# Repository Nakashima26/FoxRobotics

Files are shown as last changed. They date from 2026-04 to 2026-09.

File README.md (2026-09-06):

# WRO 2026 — Future Engineers | Self-Driving Car

> **Team:** FoxRobotics
> **| Members:** Erick Blanco · Jesse Banda · César Emiliano Ahumada
> **| Coach:** Daniel Millan
> **| Country / Region:** México — Baja California
> **| Season:** 2026

---

## Table of Contents

1. [Vehicle Overview](#1-vehicle-overview)
   - [1.1 Design goals](#11-design-goals) · [1.2 Bill of Materials](#12-bill-of-materials)
2. [Mechanical Design & Mobility](#2-mechanical-design--mobility)
   - [2.1 Chassis selection](#21-chassis-selection) · [2.2 Wheels](#22-wheels) · [2.3 Drive system (torque vs. speed)](#23-drive-system-torque-vs-speed-analysis) · [2.4 Steering](#24-steering--rack-and-pinion-with-ackermann-geometry) · [2.5 Custom parts & assembly](#25-custom-parts--assembly)
3. [Power Architecture & Sensors](#3-power-architecture--sensors)
   - [3.1 Power budget](#31-power-budget) · [3.2 Sensor selection and placement](#32-sensor-selection-and-placement) · [3.3 PCB & wiring](#33-pcb--wiring)
4. [Software Architecture](#4-software-architecture)
   - [4.1 System overview](#41-system-overview--two-controllers-one-link) · [4.2 Inter-controller protocol ("V2")](#42-inter-controller-protocol-v2) · [4.3 Vision pipeline](#43-vision-pipeline-raspberry-pi--pure_pursuit) · [4.4 Obstacle handling](#44-obstacle-handling-obstacle-challenge) · [4.5 ESP32 state machine](#45-esp32-finite-state-machine-srcesp32purepursuitpurepursuitino) · [4.6 Cascade PID](#46-cascade-pid-always-running-underneath) · [4.7 Startup handshake](#47-startup-handshake) · [4.8 Development status](#48-development-status)
5. [Systemic Thinking & Engineering Decisions](#5-systemic-thinking--engineering-decisions)
   - [5.1 Subsystem interaction map](#51-subsystem-interaction-map) · [5.2 Key engineering trade-offs](#52-key-engineering-trade-offs) · [5.3 Iteration log](#53-iteration-log) · [5.4 Risk analysis](#54-risk-analysis) · [5.5 Failure & Incident log](#55-failure--incident-log)
6. [Testing & Validation](#6-testing--validation)
   - [6.1 How we test](#61-how-we-test) · [6.2 Results to date](#62-results-to-date) · [6.3 Validation matrix](#63-validation-matrix) · [6.4 Pre-run checklist](#64-pre-run-checklist-each-venue) · [6.5 Milestones](#65-milestones)
7. [How to Build & Run](#7-how-to-build--run)
   - [7.1 Hardware](#71-hardware-requirements) · [7.2 ESP32 firmware](#72-esp32-firmware) · [7.3 Raspberry Pi software](#73-raspberry-pi-software) · [7.4 Calibration](#74-calibration-before-each-venue) · [7.5 Run](#75-run) · [7.6 Autostart & deployment](#76-autostart--deployment)
8. [Repository Structure](#8-repository-structure)
9. [Videos](#9-videos)
10. [Photos](#10-photos)

**Companion document:** [Engineering Journal](ENGINEERING_JOURNAL.md) — the dated, phase-by-phase build log, from the pre-repo design work through today, tied to commits. [§5.3 Iteration log](#53-iteration-log) and [§6.5 Milestones](#65-milestones) are the thematic views of the same history.

---

# 1. Vehicle Overview

<p align="center">
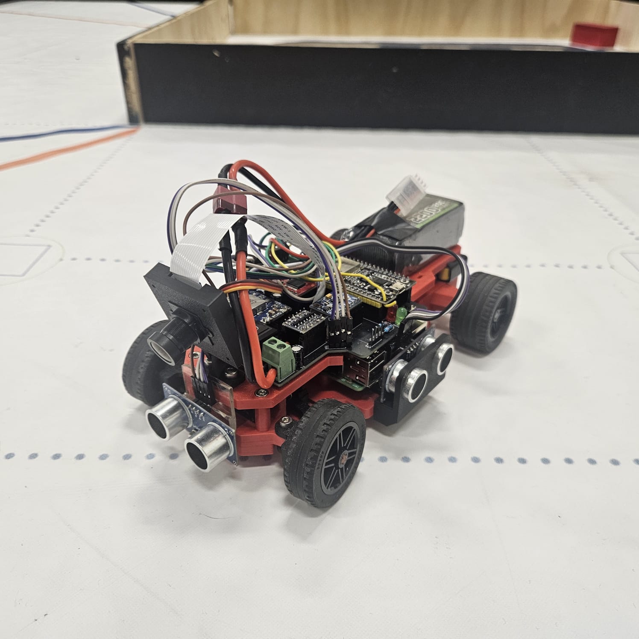
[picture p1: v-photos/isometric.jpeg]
Isometric view of the vehicle
  
</p>

Our vehicle is a custom-built autonomous car for the WRO 2026 Future Engineers — Self-Driving Cars challenge. It completes 3 laps around a randomized track, and in the Obstacle Challenge it also detects and correctly passes coloured traffic-sign pillars (**red → keep the pillar on the car's left / pass on its right; green → keep it on the right / pass on its left**) before parking at the end.

The car uses **two controllers working together**: a Raspberry Pi 4 runs the camera vision pipeline and the high-level path planner (Pure Pursuit), and an ESP32 runs the real-time control loop, the state machine and all the actuators. They talk over a UART link with a small line-based protocol ("V2"). This split is the central architectural decision of the project and is explained in [Section 4](#4-software-architecture) and [Section 5](#5-systemic-thinking--engineering-decisions).

**Key specifications:**

| Parameter | Value |
|---|---|
| Dimensions | 210 × 140 × 80 mm |
| Weight | 564 g |
| Drive type | Rear-wheel drive (RWD) |
| Steering | Ackermann rack-and-pinion, SG90 servo |
| High-level controller | Raspberry Pi 4 Model B (vision + Pure Pursuit) |
| Real-time controller | ESP32 DevKit (FSM, PID, motor & sensor I/O) |
| Inter-controller link | UART @ 115200 baud, line protocol "V2" (see §4.2) |
| Vision | Raspberry Pi Camera, NoIR wide-angle lens (FOV ≈ 120°), processed at 640 × 480 |
| Distance sensors | HC-SR04 (5V) × 3 — left, right, front — via 5V↔3.3V level shifter |
| IMU | MPU-6050 (gyroscope + accelerometer) |
| Drive motor | N20 DC gear motor (50:1) + 2:1 LEGO stage → 100:1 total |
| Motor driver | TB6612FNG |
| Battery | 3S LiPo 11.1 V 2200 mAh |
| Logic power | MINI560 step-down, 5 V |

## 1.1 Design goals

One reliable vehicle that finishes **both** challenges — scoring for completing three laps consistently over completing them fast. Everything below follows from that.

- **Fixed architecture from day one: Raspberry Pi 4 + ESP32.** The Pi does *all* image processing and vision; the ESP32 does *all* peripheral I/O — both sensing and actuation. This split was decided before the first line of code and never revisited.
- **Small footprint for maneuverability.** Comfortably inside the rulebook envelope with ~10 cm of margin on width and length — the car is ≈ 20 × 10 cm, deliberately smaller than the limit so it has room to maneuver in the obstacle field.
- **Mechanically extensible.** The chassis and the PCB were designed so components could be added later without a redesign. This paid off directly: the front ultrasonic — added for the obstacle-round segmented turn (see [§4.5](#45-esp32-finite-state-machine-srcesp32purepursuitpurepursuitino)) — went from idea to mounted-and-wired in under 30 minutes because both the chassis and the PCB already had the space and a spare header.
- **Tight-turn capable.** Rack-and-pinion steering driving both wheels symmetrically ([§2.4](#24-steering--rack-and-pinion-with-ackermann-geometry)) so the car can take the obstacle-round corners without a multi-point turn.
- **Room for a printed differential** so the rear wheels can turn at different speeds through a corner without scrub.
- **Electronics-first packaging.** The chassis was sized around the electronics — the Raspberry Pi 4 above all — and the PCB was then laid out to fit the finished mechanical model, not the other way around.

## 1.2 Bill of Materials

### Custom Manufactured Parts

| ID | Component | Description | Quantity | Supplier | Approximate Cost |
|---|---|---|---|---|---|
| 1 | BaseChasis | Main body of the vehicle. | 1 | Custom made, 3D printed | 1.6 USD |
| 2 | TopShell | Upper part of the vehicle. | 1 | Custom made, 3D printed | 1 USD |
| 3 | Cremallera | Rack used for steering. | 1 | Custom made, 3D printed | 0.1 USD |
| 4 | ServoGearDirection | Pinion for the steering system, directly connected to the servo. | 1 | Custom made, 3D printed | 0.5 USD |
| 5 | LinkageDirection | Linkage between the rack and steering knuckle. | 2 | Custom made, 3D printed | 0.05 USD |
| 6 | SteeringKnuckle | Allows lateral wheel movement for steering. | 2 | Custom made, 3D printed | 0.15 USD |
| 7 | DCsupport | Holds the DC motor in place. | 1 | Custom made, 3D printed | 0.05 USD |
| 8 | RingDifferential | Main driven gear of the differential that transfers power to the axle assembly. | 1 | Custom made, 3D printed | 0.25 USD |
| 9 | PlanetDifferential | Allows torque distribution between both wheels while enabling different wheel speeds during turns. | 2 | Custom made, 3D printed | 0.1 USD |
| 10 | PinionDifferential | Transfers rotational motion from the motor to the differential gear system. | 1 | Custom made, 3D printed | 0.1 USD |
| 11 | SunDifferential | Transfers torque from the differential gears to the wheel axle. | 2 | Custom made, 3D printed | 0.1 USD |
| 12 | CameraBase | Holds the camera frame in place. | 1 | Custom made, 3D printed | 0.1 USD |
| 13 | CameraBack | Rear section of the camera frame. Connects to the CameraBase. | 1 | Custom made, 3D printed | 0.1 USD |
| 14 | CameraFront | Camera frame. | 1 | Custom made, 3D printed | 0.2 USD |
| 15 | UltrasonicSupport | Holds an ultrasonic sensor in place (used for the left, right and front sensors). | 3 | Custom made, 3D printed | 0.3 USD |

---

### LEGO Components

| ID | Component | Description | Quantity | Supplier | Approximate Cost |
|---|---|---|---|---|---|
| 16 | Lego 6135494 | Front wheel axle. | 2 | LEGO | 0.8 USD |
| 17 | Lego 4535768 | Rear wheel axle. | 2 | LEGO | 1 USD |
| 18 | Lego 6121485 | Reduces friction on the rear wheels. | 2 | LEGO | 0.4 USD |
| 19 | Lego 4299389 | Rim for rear wheels. | 2 | LEGO | 1.2 USD |
| 20 | Lego 4184286 | Tires for rear wheels. | 2 | LEGO | 3.5 USD |
| 21 | Lego 6251174 | Rim for front wheels. | 2 | LEGO | 1.2 USD |
| 22 | Lego 6182551 | Tires for front wheels. | 2 | LEGO | 3.82 USD |

---

### Electronics

| ID | Component | Description | Quantity | Supplier | Approximate Cost |
|---|---|---|---|---|---|
| 23 | ESP32 | Real-time controller: sensor I/O, cascade PID, finite state machine, actuator PWM. | 1 | Unit Electronics | 8 USD |
| 24 | Raspberry Pi 4 Model B | High-level controller: computer vision and Pure Pursuit path planning. | 1 | Amazon | 60 USD |
| 25 | Mini560 5V | Step-down regulator powering the Raspberry Pi, ESP32 and peripherals. | 1 | Amazon | 6 USD |
| 26 | MPU 6050 | 6-axis IMU used to measure angular velocity and integrate heading. | 1 | Unit Electronics | 3 USD |
| 27 | HC-SR04 | Ultrasonic distance sensors — left, right (wall following) and front (obstacle-round cornering). | 3 | Unit Electronics | 10.5 USD |
| 28 | Level Shifter | Logic-level converter for the 5 V HC-SR04 echo lines into the 3.3 V ESP32. | 1 | Unit Electronics | 7 USD |
| 29 | Driver TB6612FNG | Motor driver controlling speed and direction of the DC drive motor. | 1 | Unit Electronics | 5 USD |
| 30 | RaspiCamera V2 | Camera module used for computer vision. | 1 | Amazon | 10 USD |
| 31 | Custom PCB | Printed circuit board for power distribution and electronic connections. | 1 | JLCPCB | 5 USD |

---

### Power System

| ID | Component | Description | Quantity | Supplier | Approximate Cost |
|---|---|---|---|---|---|
| 32 | Ovonic 2200mAh 3S | 3-cell LiPo battery powering the robot's electronics and drive system. | 1 | E-Bay | 13 USD |

---

### Actuators

| ID | Component | Description | Quantity | Supplier | Approximate Cost |
|---|---|---|---|---|---|
| 33 | N20 with 50:1 reduction | DC gear motor providing torque for robot movement. | 1 | Unit Electronics | 6 USD |
| 34 | SG90 Servo | Micro servo motor used for steering control. | 1 | Unit Electronics | 6 USD |

---

### Fasteners

| ID | Component | Description | Quantity | Supplier | Approximate Cost |
|---|---|---|---|---|---|
| 35 | M3 Screws | Used for structural assembly and component mounting. | 23 | Local Hardware Store | 1 USD |
| 36 | M3 Nuts | Used to secure structural and electronic components. | 1 | Local Hardware Store | 0.05 USD |
| 37 | M2 Nuts | Used to secure servo motor and servo pinion | 3 | Local Hardware Store | 0.15 USD |

### Total Estimated Cost

| Total |
|---|
| ~155 USD |

---

# 2. Mechanical Design & Mobility

### 2.1 Chassis selection

The chassis was designed from scratch to fit all the components we needed for competition. We printed it in red and black SUNLU PLA on a Bambu Lab A1, keeping the structure as light as possible without sacrificing the rigidity the drivetrain and electronics require.

For wheel transmission shafts, we used LEGO axles throughout: part 6135494 for the front and part 4535768 for the rear. This wasn't an aesthetic choice — LEGO axles have much better dimensional consistency than fully printed shafts, which flex under load and cause alignment issues. We also added LEGO bushings (6121485) to the rear axle to cut down on friction between moving parts.

| Component | Material / Part | Purpose |
| --- | --- | --- |
| Chassis | SUNLU PLA | Main robot structure |
| Front Axles | LEGO 6135494 | Power transmission |
| Rear Axles  | LEGO 4535768 | Rear drivetrain support |
| Bushings | LEGO 6121485 | Friction reduction |
| Printer | Bambu Lab A1 | Manufacturing process |

We used PLA because it prints fast, doesn't warp like ABS, and is stiff enough for indoor competition conditions. PETG has better impact resistance and ABS handles heat better, but neither of those properties matters much for a robot running on a flat mat indoors. What did matter was being able to iterate quickly and get consistent parts, and PLA delivered on both.

### 2.2 Wheels

We tested several wheel options before settling on LEGO parts. The rear wheels use rim 4299389 with tire 4184286, and the front uses rim 6251174 with tire 6182551. Both have a 43 mm outer diameter, which keeps the ride height even front to rear.

Since the drivetrain already uses LEGO axles, LEGO-compatible rims were the obvious fit — they mount directly without adapters, which removes a potential source of wobble at the wheel interface.

The 43 mm diameter was also validated against our motor RPM target. At our gear ratio, this diameter puts normal operation in the 40–70% PWM range, which gives us enough resolution for smooth speed control. A noticeably larger wheel would push operating duty cycles above 85% and compress the usable throttle range.

We ran the car at full throttle on the competition mat surface and saw no detectable slip at the rear. The LEGO rubber compound grips the white matte WRO field without any prep needed.

### 2.3 Drive system (torque vs. speed analysis)

The main drive is an N20 DC motor with a 50:1 internal gearbox — compact at 12 × 10 × 26 mm and still enough torque for a ~1.5 kg vehicle. Between the motor output shaft and the differential, we added a 2:1 LEGO gear stage, bringing the total drivetrain reduction to **100:1** and estimated rear axle torque to about 1.76 kg·cm.

**Why 100:1 and not just 50:1?**

We ran the 50:1 configuration first. It was faster, but corner exits were inconsistent — the rear wheels would occasionally lose traction under acceleration, causing yaw disturbances the PID couldn't fully catch. At 100:1, top speed dropped but torque delivery became smooth and predictable all the way through the speed range. Corner exits became repeatable, which turned out to be a prerequisite for reliable PID tuning.

The ratio also keeps the motor in its efficient RPM band during most of the run, which matters because the motor shares a power source with the logic rail.

The car completes all three Open Challenge laps in about 12 seconds at just 60% motor speed. That headroom is useful if we need to push speed in later iterations.

**The takeaway:** we prioritized consistency over raw speed. A robot that reliably finishes 3 laps scores more than one that's faster but unpredictable.

### 2.4 Steering — rack-and-pinion with Ackermann geometry

Steering is controlled by an SG90 servo connected to both front knuckles through a rack-and-pinion mechanism with symmetric tie rods.

**Mechanism specs:**

| Parameter | Value |
|---|---|
| Servo | SG90 (0°–180° range) |
| Firmware straight-ahead trim | 80° (servo-horn spline offset; `centroServo` in firmware) |
| Pinion | Module 1, 14 teeth |
| Pinion pitch diameter | 14 mm (dp = m × z = 1 × 14) |
| Pinion outer diameter | 16 mm (dp + 2×addendum = 14 + 2) |
| Rack | Module 1, 11 teeth, 27.5 mm total travel |
| Rack displacement per servo degree | 0.1222 mm/° |
| Transmission ratio | 2.50° servo : 1° wheel |
| Geometric wheel steering range | ±43° from center |
| Firmware-clamped servo command | 20°–150° (≈ ±35° usable at the wheel) |

**Kinematic analysis:**

The 14 mm pitch diameter gives a pitch circumference of 43.98 mm. Each degree of servo rotation moves the rack 0.1222 mm. At 90° per side from center, the rack travels 11.00 mm per side — producing ±43° at the front wheels.

The outer diameter of 16 mm confirms the module (d_outer = dp + 2×m = 14 + 2 = 16 mm).

The 2.50:1 ratio reduces steering sensitivity at the wheel, which gives the inner control loop finer resolution at its update rate. A lower ratio would make steering response too abrupt.

The firmware never commands the full mechanical range: `escribirServo()` is clamped to 20°–150° (about ±35° at the wheel) so a saturated control output can't drive the rack into its physical end stop. That still clears the tightest Open-Challenge corridor (600 mm) and the maneuvering the Obstacle Challenge needs.

**Why rack-and-pinion over a direct servo arm?**

A direct arm only controls one wheel directly. The opposite knuckle, linked by a fixed-length tie rod, gets an angle that's geometrically correct only at center — producing toe error everywhere else. The rack pushes both tie rods symmetrically, so both wheels get the right angle at every steering position. Combined with the Ackermann geometry of the knuckles, each wheel tracks its own correct turning radius. No lateral scrub, and steering response is linear across the full range.

### 2.5 Custom parts & assembly

Every structural part is 3D-printed in SUNLU PLA on a Bambu Lab A1. The mechanical model was built first; the PCB was then laid out to fit it. Editable SolidWorks parts are in [`models/CAD/`](models/CAD/), printable meshes in [`models/STL/`](models/STL/), isometric renders in [`models/renders/`](models/renders/).

<p align="center">
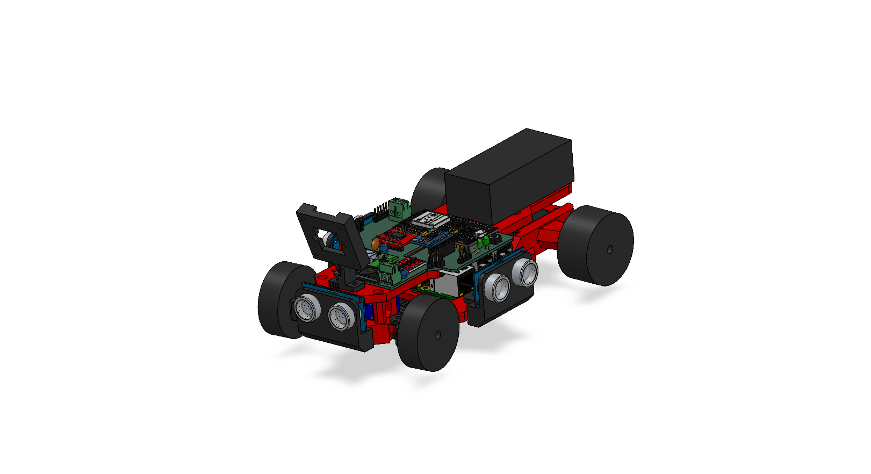
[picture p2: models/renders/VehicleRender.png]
Full vehicle CAD assembly
  
</p>

| Render | Part | Function / design note |
|---|---|---|
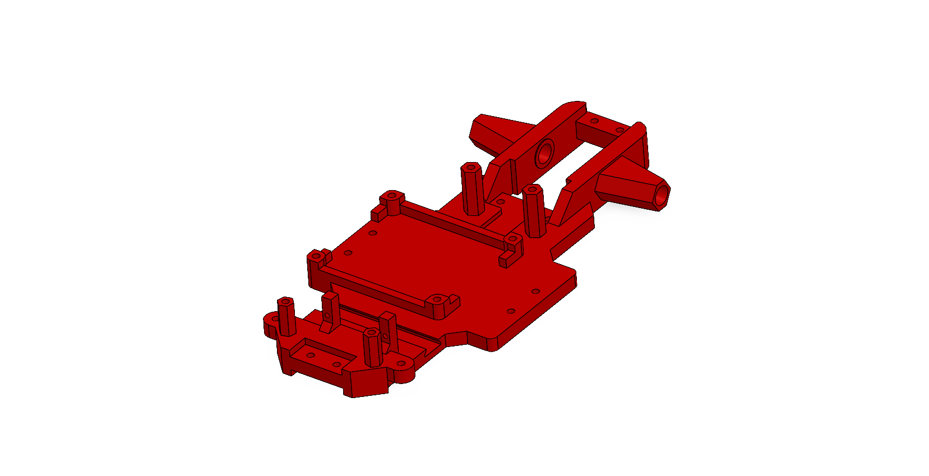
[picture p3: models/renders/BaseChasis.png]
BaseChasis render
|  | **BaseChasis** | Main structure. Sized around the electronics (Raspberry Pi 4 first); carries the PCB, steering, drivetrain and every sensor mount. |
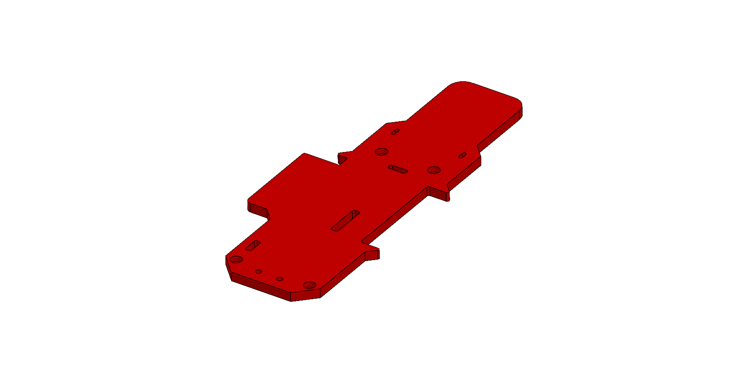
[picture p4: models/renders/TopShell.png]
TopShell render
|  | **TopShell** | Top cover — closes the electronics bay and protects the wiring. |
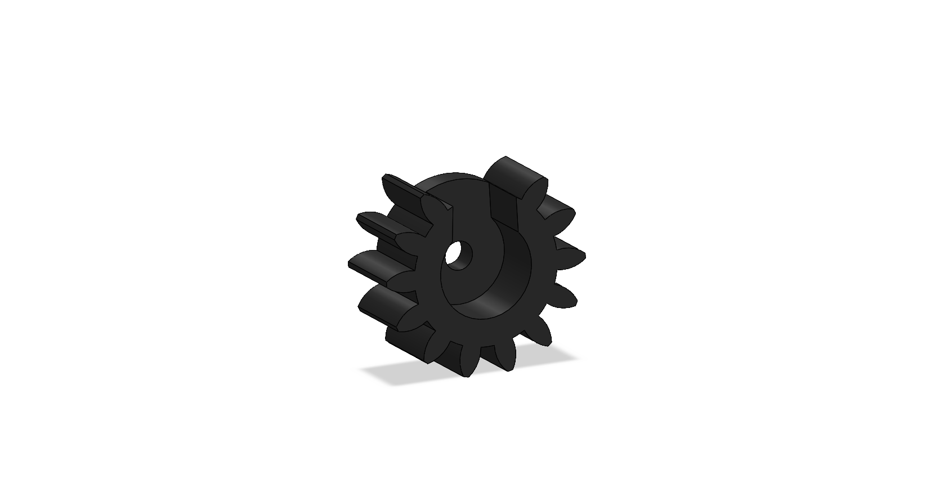
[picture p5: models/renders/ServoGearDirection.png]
ServoGearDirection render
|  | **ServoGearDirection** | Pinion pressed onto the SG90 output shaft — module 1, 14 teeth. |
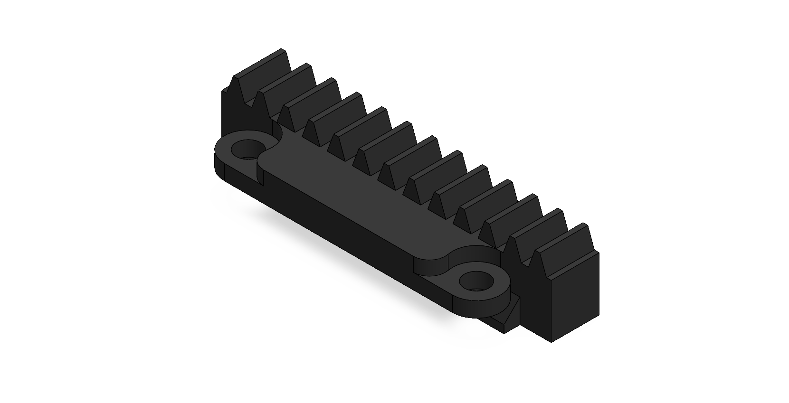
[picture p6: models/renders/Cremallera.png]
Cremallera render
|  | **Cremallera** (rack) | Module 1, 11 teeth, 27.5 mm travel. Converts servo rotation into lateral travel for the tie rods. |
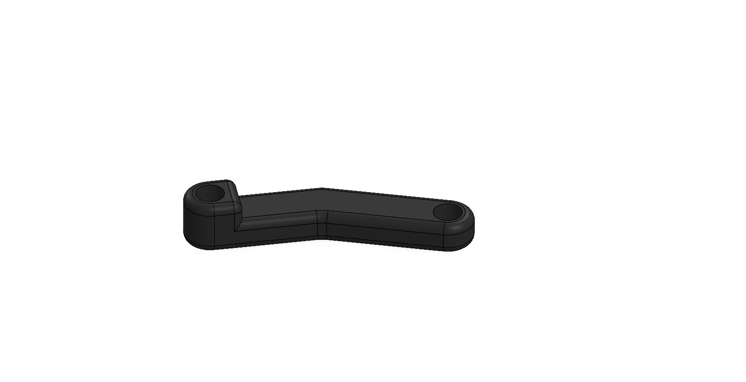
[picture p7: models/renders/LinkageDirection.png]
LinkageDirection render
|  | **LinkageDirection** ×2 | Tie rods from the rack ends to the steering knuckles — symmetric, so both wheels get the correct angle at every rack position. |
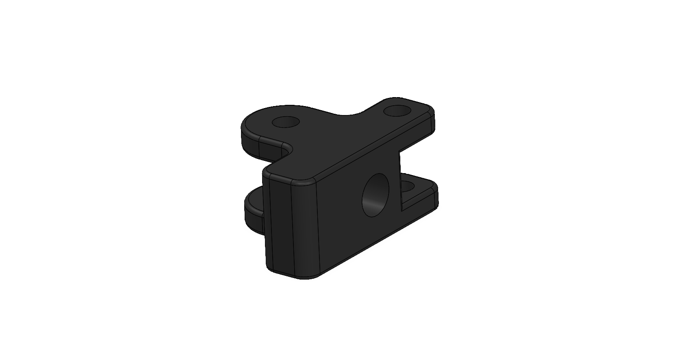
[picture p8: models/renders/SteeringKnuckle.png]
SteeringKnuckle render
|  | **SteeringKnuckle** ×2 | Front-wheel pivots; their geometry sets the Ackermann steering angles. |
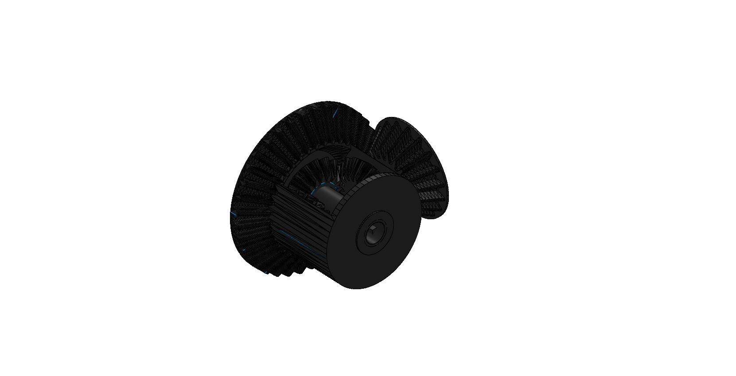
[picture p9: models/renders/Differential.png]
Differential render
|  | **Differential** (Ring / Planet ×2 / Pinion / Sun) | Printed open differential — lets the rear wheels turn at different speeds through a corner. |
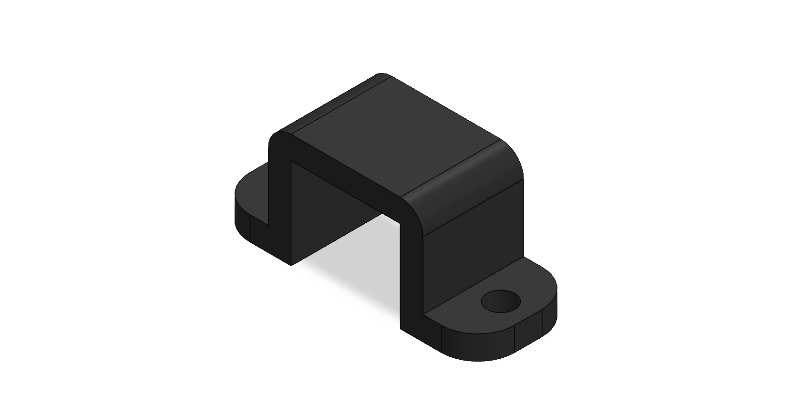
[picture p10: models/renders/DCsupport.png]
DCsupport render
|  | **DCsupport** | Mounts the N20 gear motor to the chassis. |
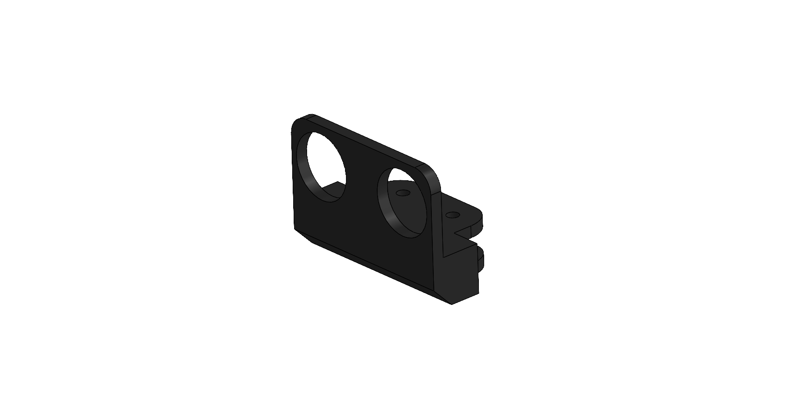
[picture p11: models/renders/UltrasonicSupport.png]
UltrasonicSupport render
|  | **UltrasonicSupport** ×3 | Two identical side mounts; one slightly smaller front mount, added later for the obstacle-round segmented turn. |
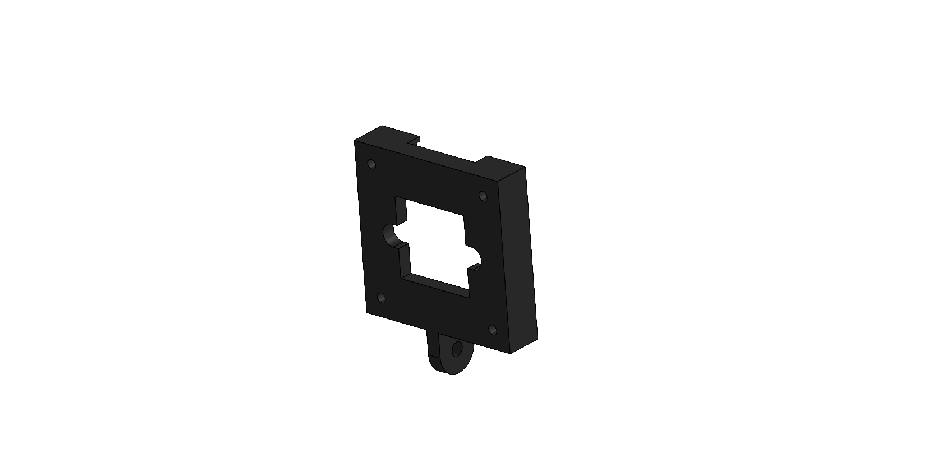
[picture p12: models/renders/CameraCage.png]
Camera cage render
|  | **CameraHold** | Structure in charge of holding the camera. Sets the fixed ~15° downward tilt the BEV homography is calibrated against ([§3.2](#32-sensor-selection-and-placement)). |

#### Assembly order

1. **Chassis base** — the reference part everything mounts to.
2. **Steering** — press the pinion onto the servo and seat the servo in the chassis; slide in the rack; link each rack end to a SteeringKnuckle with a LinkageDirection tie rod; fit the knuckles and the front LEGO axles.
3. **Drivetrain** — N20 motor into the DCsupport; assemble the printed differential; rear LEGO axles with bushings.
4. **Sensor mounts** — the two side UltrasonicSupports (identical) and the smaller front one; the camera cage (base + back + front) with the camera.
5. **Electronics** — PCB onto the chassis bosses; wire the Pi 4, ESP32, the three HC-SR04 (through the level shifter), the MPU-6050, the TB6612 + motor, the servo, and the start button + status LED.
6. **TopShell** — close the bay.

All fasteners are M3 (M2 nuts on the servo horn and pinion).

---

# 3. Power Architecture & Sensors

### 3.1 Power budget

The whole vehicle runs off an Ovonic 2200mAh 3S LiPo. Power splits two ways: the motor driver takes battery voltage directly for the DC motor, and everything else goes through a MINI560 step-down converter producing a stable 5V at up to 5A.

| Rail | Source | Consumers | Max Current Draw |
|---|---|---|---|
| 5V Logic | MINI560 Step-Down Converter | Raspberry Pi 4 + RaspiCam V2, ESP32, HC-SR04 ×3, MPU6050, SG90 | ~4.0 A |
| Battery / Main Power | Ovonic 2200mAh 3S LiPo | Entire vehicle power distribution | ~35 A discharge capability |
| Motor Power | Motor Driver directly from 3S LiPo | DC drive motor | ~1.6 A peak |
| 3.3V Internal | ESP32 internal regulator | I²C communication and internal ESP32 logic, Level Shifter | ~200 mA |

The Ovonic battery is rated 120C continuous, which is theoretically 264 A. We're drawing about 4.5 A peak — under 2% of its discharge capability. There's no shortage of headroom here.

The Raspberry Pi and the ESP32 share the 5 V rail but the DC motor is fed straight from the battery through the TB6612FNG, so stall-current spikes on the motor never sag the logic supply.

### 3.2 Sensor selection and placement

| Sensor | Purpose | Placement | Notes |
|---|---|---|---|
| Raspberry Pi Camera Module V2 | Lane, corner-line and pillar detection | Front-center, ~15° downward tilt | Main vision system, OpenCV on the Pi |
| HC-SR04 (left) | Left wall distance | Left side of the chassis | Feeds the wall-centering PID |
| HC-SR04 (right) | Right wall distance | Right side of the chassis | Feeds the wall-centering PID |
| HC-SR04 (front) | Distance to the wall ahead when approaching a corner | Front bumper, facing forward | Obstacle round only — triggers the CRUCERO → MANIOBRA sequence |
| MPU-6050 | Heading integration during cornering and recovery | Center of chassis | Gyro Z integrated into `anguloGyro`, echoed back to the Pi |

#### Camera system

The camera handles lane geometry (via a bird's-eye-view transform), the orange corner-line markers, and red/green pillar detection. Image processing runs on the Raspberry Pi 4 with OpenCV in real time and drives the Pure Pursuit planner.

It is mounted front-center with a ~15° downward tilt. We tested a horizontal mount first, but that captured too much background, which slowed detection and added noise. Tilting it down focuses the field of view on the track and the obstacle zone, which cut both false positives and computational load. The exact tilt is baked into the bird's-eye-view homography during calibration (see §4.3), so the mount must not move after calibration.

The lens is a wide-angle **NoIR** unit (~120° FOV), chosen over the original ~63° lens so the camera sees far enough ahead to react to a pillar and read the corner on the same frame. The wide lens ships without an IR-cut filter, which gave the raw image a heavy red cast and broke every HSV mask. The libcamera capture pipeline pins white-balance instead of letting it float — `libcamerasrc awb-enable=false colour-gains=<1.2,1.5>` — so the correction holds across venue lighting, and the pillar HSV ranges were re-tuned on the corrected image (see [ERR-03](#err-03--wide-angle-noir-lens-put-a-red-cast-on-every-frame)).

#### HC-SR04 ultrasonic sensors

The left and right sensors drive lateral positioning and wall following. The **front** sensor was added for the Obstacle Challenge: because that round uses a segmented, stop-and-maneuver turn instead of a continuous arc (see §4.5), the car needs to know how far it is from the wall ahead so it can decide *when* to stop cruising and *which* maneuver (forward arc or reverse pivot) to run.

We originally tested VL53L0X time-of-flight sensors. On paper they win — ±3 mm accuracy versus ±15 mm for the HC-SR04, and a narrower beam. In practice, the black competition walls absorbed their 940 nm IR signal and consistently returned out-of-range readings at 300 mm. The HC-SR04 reflects off any surface regardless of color. We went with reliability over precision and made up the accuracy difference with software filtering (EMA on all three channels, plus a 5-sample median on the front channel to reject spikes before they can trigger a maneuver).

#### MPU-6050 IMU

The MPU-6050 gives heading and rotation data during cornering and recovery. The gyro Z axis is integrated each loop into `anguloGyro`, with a 1°/s deadband to suppress MEMS thermal drift on straights. On startup the firmware averages several hundred stationary samples to compute the gyro bias (`calcGyroOffsets`); if that offset comes back unusually large the firmware halves the integration scale as a safety net. The integrated heading is also sent back to the Pi in every acknowledgement so the vision side can dead-reckon obstacle positions (see §4.4).

### 3.3 PCB & wiring

A custom two-layer PCB is the vehicle's backplane: it distributes power and carries every signal line between the ESP32, the sensors and the motor driver, so there is no breadboard or flying-wire harness to work loose. This is what let the front ultrasonic go in in under 30 minutes ([§1.1](#11-design-goals)) — the header was already there. The full editable KiCad project is in [`electrical/WRO_RevA/`](electrical/WRO_RevA/).

**Schematic** ([`schemes/schematic.png`](schemes/schematic.png)):

<p align="center">
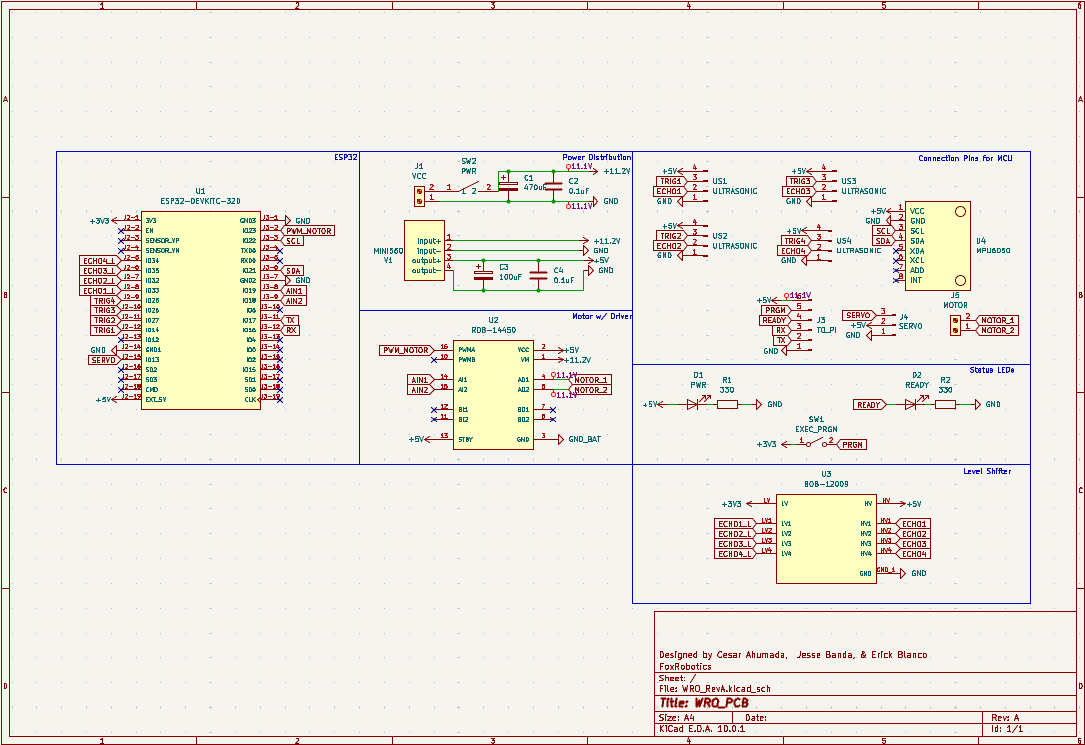
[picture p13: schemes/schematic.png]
KiCad schematic
  
</p>

The ESP32 DevKit (`U1`) sits at the centre. Battery voltage (~11.1 V, 3S) comes in at the `VCC` screw terminal (`J1`) and splits two ways: the motor driver takes it directly, and a MINI560 buck (`V1`, bulk caps `C1`–`C4`) drops it to the 5 V logic rail. The RDB-14450 driver (`U2`) takes `PWM_MOTOR` / `AIN1` / `AIN2` from the ESP32 and drives `MOTOR_1/2` out to the screw terminal `J5`. The four HC-SR04s land on headers `US1`–`US4` (5 V / TRIG / ECHO / GND); their 5 V echo lines return through a BOB-12009 level shifter (`U3`) that steps `ECHO1`–`ECHO4` down to 3.3 V for the ESP32. The MPU-6050 (`U4`) is on I²C. The `TO_PI` header (`J3`) is the entire link to the Raspberry Pi — `RX` / `TX` for the V2 protocol, `READY` for the handshake, `PRGN` for the start button (`SW1`), plus 3.3 V / GND. Two status LEDs (`D1` PWR, `D2` READY) complete the operator interface from [§4.7](#47-startup-handshake).

**Populated board** ([`schemes/pcb_render.png`](schemes/pcb_render.png)):

<p align="center">
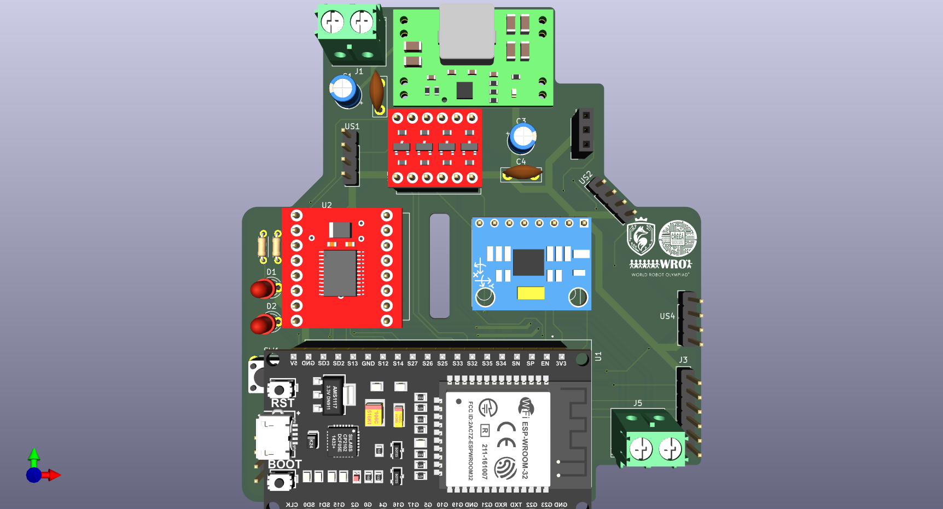
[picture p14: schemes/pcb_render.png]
3D render of the populated PCB
  
</p>

**Board outline** ([`electrical/PCB_dimensions.png`](electrical/PCB_dimensions.png)):

<p align="center">
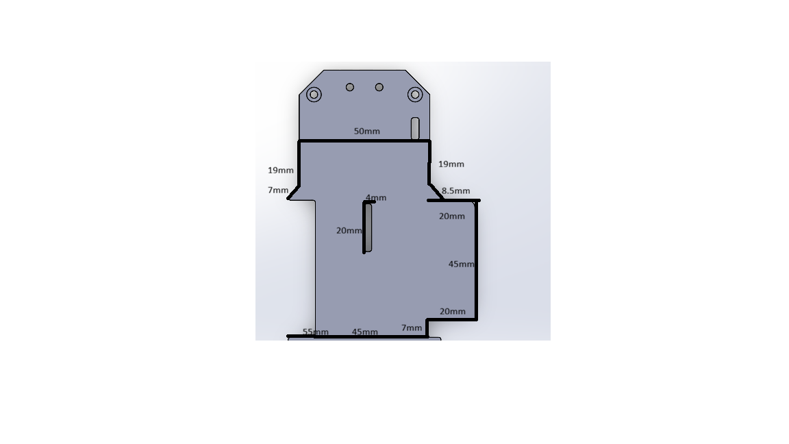
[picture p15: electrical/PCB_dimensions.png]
PCB outline and dimensions
  
</p>

The board is a custom non-rectangular shape (~55 mm at its widest) that nests into the chassis around the Raspberry Pi 4 and the drivetrain — the electronics-first packaging from [§1.1](#11-design-goals) in physical form. The cut-outs and the mounting-hole row let the PCB, the steering and the sensor mounts share one footprint without stacking height.

---

# 4. Software Architecture

### 4.1 System overview — two controllers, one link

Responsibility is split across two processors by hardware strength:

```
        RASPBERRY PI 4 (Python, OpenCV)                          ESP32 (Arduino / C++)
 ┌───────────────────────────────────────────┐    V2     ┌────────────────────────────────────┐
 │ Camera → BEV homography → floor centerline│   UART    │ readPiSerial()  →  parse V2        │
 │ Pillar detection (HSV) + corner-line track│  ──────►  │                                    │
 │ Rolling obstacle memory (dead reckoning)  │  115200   │ 6-state FSM                        │
 │ Pure Pursuit geometric controller         │           │  SIGUIENDO / GIRANDO / RECUPERANDO │
 │ RECUPERANDO trigger (measured state)      │  ◄──────  │  CRUCERO / MANIOBRA / TERMINANDO   │
 │ builds one V2 line per processed frame    │  ACK:V2   │ cascade PID (wall + gyro)          │
 └───────────────────────────────────────────┘   ang=    │ servo + motor PWM, HC-SR04, MPU    │
                                               est= dir= └────────────────────────────────────┘
```

- The **Pi** decides *where to steer*: it turns the camera frame into a top-down view, extracts a drivable centerline, runs a Pure Pursuit controller against it, and reduces the result to a single normalized steering value plus a few status flags. It processes 1 of every 3 captured frames (~12–15 Hz effective).
- The **ESP32** decides *how to drive*: it owns the 50 Hz control loop, the finite state machine, corner detection, the recovery behaviour, and every actuator. In the Obstacle round it treats the Pi's steering value as the primary reference while Pure Pursuit is active, and falls back to its own wall + gyro PID if the Pi goes silent for more than 800 ms. In the Open round it ignores the Pi's steer altogether and runs on wall + gyro PID the whole time (§4.5).

Why not one processor? Real-time GPIO timing (ultrasonic pulses, servo/motor PWM, gyro sampling) and non-deterministic OpenCV latency don't coexist well on one core. Linux can't guarantee a µs-accurate pulse while an HSV pass is running; a microcontroller can't run OpenCV. Splitting them lets each run at its own natural rate, and a late UART packet just means the ESP32 reuses the last command instead of stalling. This trade-off is analyzed in [Section 5](#5-systemic-thinking--engineering-decisions).

**Where to start reading the code:** the Pi loop is [`pure_pursuit/runtime_nuevo.py`](src/RASPI/cam/pure_pursuit/runtime_nuevo.py) (`run()` → per-frame block); the ESP32 loop is [`PurePursuit.ino`](src/ESP32/PurePursuit/PurePursuit.ino) (`loop()` → the `switch (estado)`). Every module is annotated in [Section 8](#8-repository-structure); tunables live in [`pure_pursuit/config.py`](src/RASPI/cam/pure_pursuit/config.py).

### 4.2 Inter-controller protocol ("V2")

One line per processed frame, newline-terminated, 115200 baud. The rest of Section 4 refers to these fields by name.

**Pi → ESP32:**

```
V2,obs=+0.123,turn=0,state=pp,prio=1,mem=18,pp=1,pasado=0,intr=0
```

| Field | Meaning |
|---|---|
| `obs` | Normalized steering, `steer_deg / 60`, range −1…+1 (`+` = right). |
| `turn` | Legacy directional hint — always `0`; turn direction is resolved on the ESP32 side. |
| `state` | Human-readable label for the journal (e.g. `pp`, `avoid_red`). |
| `prio` | `1` = an obstacle is actively being avoided → **ESP32 must not start a corner turn**. |
| `mem` | Frames of obstacle memory still live → also blocks corner detection while `> 0`. |
| `pp` | `1` = Pure Pursuit steering is authoritative (suspend the wall PID). |
| `pasado` | One-frame pulse: the Pi confirms the car has *physically* cleared an obstacle → enter RECUPERANDO. |
| `intr` | Interior-pass flag (disabled by default). |

**ESP32 → Pi:**

```
ACK:V2,ang=12.34,est=S,dir=L,...debug...
```

| Field | Meaning |
|---|---|
| `ang` | Integrated IMU heading `anguloGyro` (degrees); resets to 0 at each turn. |
| `est` | FSM state — `S` SIGUIENDO, `G` GIRANDO **or** MANIOBRA, `R` RECUPERANDO, `C` CRUCERO. |
| `dir` | Track turn direction — `?` until the first turn, then `L` / `R`. |

### 4.3 Vision pipeline (Raspberry Pi — `pure_pursuit/`)

Entry point: `pure_pursuit/runtime_nuevo.py`. Per processed frame:

1. **Capture** — a threaded grabber pulls frames from the Pi camera through a libcamera/GStreamer pipeline at 640 × 480 BGR, dropping stale buffers so the loop always sees the newest frame.
2. **Bird's-eye view (`bev.py`)** — a homography (inverse-perspective mapping) warps the camera frame to a top-down 400 × 400 image at 2 mm/px. The homography comes from `bev_calib.npz`, generated once by `calibrate.py` from a **3 × 3 grid of 9 physical floor markers** (RANSAC fit). We use 9 points, not the minimum 4: a 4-point fit is exact and can't detect a mis-click or extrapolate safely beyond the marked area, while 9 points let the solver average out click noise across the full range the centerline actually uses (from just ahead of the car out to ~550 mm).
3. **Pillar detection (`vision.py`)** — HSV masks for red and green, then contour filtering by area, **solidity** (compact blob ≈ 0.7–0.9, painted line < 0.4) and **aspect ratio** (< 2.2) so the mat's coloured lines are not mistaken for pillars.
4. **Centerline (`centerline.py`)** — a floor-colour mask in the BEV, minus inflated "keep-out" disks around each obstacle. The keep-out is **asymmetric per the WRO rule**: a red pillar inflates further to its *left* (car passes on the right), a green pillar further to its *right*. Rows are sampled bottom-to-top; each row blends the free-gap center with the WRO pass-side using a weight that ramps up as the car nears the can (not a binary switch). A 1-D moving average plus a per-step Δx clamp keep the path within the servo's curvature limit.
5. **Pure Pursuit (`controller.py`)** — a geometric pure-pursuit controller in BEV pixel space. Look-ahead is **adaptive**: it shrinks from 100 px toward 78 px as the nearest can closes *longitudinally*, so the car keeps translating and arcs around the can instead of pivoting in place. Output is slew-limited to 6°/frame to kill frame-to-frame steering whip.
6. **Serialize** — the steering angle is normalized (`obs = steer_deg / 60`) and packed into one V2 line with the status flags (§4.2).

```mermaid
flowchart TB
    A["Capture — threaded grabber<br/>Pi camera 640×480 BGR, drops stale buffers"]
    B["BEV homography (bev.py)<br/>IPM warp to 400×400 top-down, 2 mm/px<br/>from bev_calib.npz (9-point RANSAC)"]
    C["Pillar detection (vision.py)<br/>HSV red/green + area + solidity + aspect ratio"]
    D["Centerline (centerline.py)<br/>floor mask minus asymmetric keep-out disks<br/>red inflates left, green inflates right<br/>pass-side weight ramps with distance"]
    E["Rolling obstacle memory (obstacle_memory.py)<br/>ego-motion: assumed speed + real IMU heading from ACK<br/>confidence decay, prune-on-pass"]
    F{"Measured RECUPERANDO trigger<br/>ARM / CLEAR / SKEW — see §4.4"}
    G["Pure Pursuit (controller.py)<br/>geometric, look-ahead 100 to 78 px adaptive<br/>slew-limited 6°/frame"]
    H["Serialize one V2 line<br/>obs = steer_deg / 60, plus prio / mem / pp / pasado"]
    A --> B
    B --> C
    B --> D
    C --> E
    E --> D
    E --> F
    D --> G
    G --> H
    F --> H
    H --> Z(["UART to ESP32 @ 115200"])
```

#### How the Pure Pursuit controller works

Pure Pursuit is a path-tracking method: instead of reacting to an *error signal*, the controller looks a fixed distance ahead along the path — the **look-ahead** — picks the point on the centerline at that distance, and computes the single steering angle whose turning arc, starting from the car's current pose, passes exactly through that point. Every frame the target point moves forward along the centerline and the car "chases" it, so the trajectory is always a smooth arc onto the path rather than a hand-tuned reaction curve.

```
          centerline (from BEV)                 look-ahead point picked at
        ·····•·····•·····•···•···•  ← target    distance  ld  along the path
                            ╲
                             ╲  arc the steering angle produces
              ┌───┐           ╲
              │car│────────────•   robot pose (rear axle = reference)
              └───┘
                 └─ α = bearing to target,  steer = atan2(2·L·sin α, ld)
```

Why it fits this problem:

- The vision pipeline already produces a **path** (the centerline), not a point to servo onto — Pure Pursuit consumes that path directly.
- The look-ahead is a single, physically meaningful tuning knob: **short = cut hard toward the path** (fast dodge), **long = ease onto it** (smooth cruise). That is exactly the behaviour the obstacle logic needs, so avoidance is folded into the *same* controller by shrinking the look-ahead near a can instead of adding a separate avoidance mode.
- It degrades gracefully: a noisy or short path just moves the target point a little; there is no integrator to wind up and no error term to spike.

```python
dx = target[0] - robot_x          # lateral offset to the look-ahead point (BEV px)
dy = robot_y - target[1]          # forward distance to it
ld = max(1.0, math.hypot(dx, dy)) # actual chord length
alpha     = math.atan2(dx, dy)                                   # bearing to the point
steer_rad = math.atan2(2.0 * C.WHEELBASE_PX * math.sin(alpha), ld)  # pure-pursuit arc
steer_deg = math.degrees(steer_rad)

if bev_obstacles:                                   # a can is in play
    steer_deg *= self._distance_steer_gain(...)     # ramp 0.30→1.0 as it closes
steer_deg = max(-C.MAX_STEER_DEG, min(C.MAX_STEER_DEG, steer_deg))
steer_deg = clamp(steer_deg, prev ± C.PP_STEER_SLEW_DEG)   # 6°/frame slew limit
```

`adaptive_lookahead` shrinks the look-ahead from 100 px toward 78 px, and `_distance_steer_gain` ramps the steering scale from 0.30 up to 1.0, both as the nearest can closes. Both key off the **longitudinal** distance to the can (forward gap), not the Euclidean one: a can still off to the side but level with the car used to keep those values relaxed, and the car drove straight past the point where it should have started turning. The WRO pass-side bias (right of red, left of green) is *not* handled here — it is already baked into the centerline by `centerline.py`, so the controller only has to follow the path it is given.

If `bev_calib.npz` is missing, the runtime falls back to a simple reactive PID on the pillar's x-position in the raw frame (`RED_TARGET_PX` / `GREEN_TARGET_PX`) so the car is never left without a controller.

### 4.4 Obstacle handling (Obstacle Challenge)

**Rolling obstacle memory (`obstacle_memory.py`).** The BEV only contains what the camera sees *now*; as the car closes on a can, the can leaves the bottom of the frame, its keep-out disc vanishes, and the centerline snaps back to center — cutting the corner onto the can. The memory fixes this: seen cans are stored as `(x, y, colour, confidence)` in robot-relative BEV coordinates and, every frame, the ego-motion is applied to every remembered can — forward travel from an assumed speed, rotation from the **real IMU heading change** in the ESP32 acknowledgement:

```python
dheading = heading_deg - self._prev_heading          # real Δ from the ACK, degrees
ds_px    = (C.ROBOT_SPEED_MMS * dt_s) / C.MM_PER_PX  # assumed forward advance, BEV px
# a hard dodge rotates the car without translating it — shrink ds_px when |dheading| is large
ds_px   *= turn_brake(dheading)
self._advance(ds_px, dheading)     # each can: y += ds_px, then rotate −dheading about the robot
```

Fresh detections are merged in, unseen cans decay in confidence and are pruned once genuinely passed. The inflated keep-out therefore persists until the car has physically cleared the can. The `heading_deg` this relies on is exactly the value the ESP32 integrates for its own control (see §4.6) and echoes back — one shared heading, so the map rotates by the same angle the car actually turned.

**"Mine" vs "beyond the corner" (`corner_lines.py`).** The mat's orange corner lines are tracked row-by-row in the BEV. Each remembered can is classified as *mine* (on my straight, must be avoided) or *beyond* (on the next straight, ignore for now), with asymmetric hysteresis — quick to start avoiding, slow to stop — because starting to dodge is the safe side of a wrong call.

**Far hint (`far_hint.py`).** A PD controller on a pillar's offset in the *raw* camera frame (before it projects into the BEV range) nudges the steering to pre-center on a distant can, capped at ±12° so it can only hint, never dodge.

**Mid-turn detector (`mid_turn.py`).** While the ESP32 is turning, the rolling memory is disabled (its motion model assumes forward travel, which a pivot violates). This detector instead uses only the raw per-frame BEV projections and requires a same-colour can in a consistent position across several frames inside a close forward cone to "confirm" it. **Phase 1 (current): observe and log only** — it writes `[MTURN]` lines to the journal and does not yet change steering, so we can measure its reliability on-track before wiring it into the firmware.

#### Triggering RECUPERANDO from the obstacle memory

**The problem.** When the car has to swing wide around a can with no room to spare, it finishes the pass **crooked** — pointing 30–60° off the straight — and often with one wall out of ultrasonic range. At that exact moment the camera view is the least trustworthy (the centerline is short and skewed), so letting Pure Pursuit "straighten itself" from what it sees tends to over- or under-correct into a wall. The fix is to hand the wheel to the ESP32's wall + gyro PID (state `RECUPERANDO`) until the chassis is realigned — but *only* for a hard dodge. A gentle dodge with space to spare straightens itself fine and should not stop for a recovery.

**The trigger** (`_measured_recup_trigger` in [`runtime_nuevo.py`](src/RASPI/cam/pure_pursuit/runtime_nuevo.py)) does not dead-reckon the can itself — it reads the state the obstacle memory and the IMU already provide, and needs three things to line up:

```
1. ARM   a real dodge is in progress:
         the centerline's avoidance weight near the car's axis has been
         ≥ RECUP_MEAS_ARM_W for RECUP_MEAS_ARM_FRAMES straight frames.
         On arming, snapshot heading_ref = current heading (the straight's heading).

2. CLEAR the memory no longer places any Red/Green can both far enough ahead
         of the axis AND close enough to the side to be in the way
         (going straight, the car's edge would clear it) — held for
         RECUP_MEAS_CLEAR_FRAMES frames (or just 1 if a corner is imminent).

3. SKEW  |heading − heading_ref| ≥ RECUP_MEAS_HEADING_DEG   (25°)
         → there is actually something to straighten.

ARM && CLEAR && SKEW  →  emit pasado=1  (one-frame pulse)  →  ESP32 enters RECUPERANDO
CLEAR but never SKEW for RECUP_MEAS_GENTLE_FRAMES  →  disarm quietly, no RECUPERANDO
```

```mermaid
flowchart TB
    S(["Each processed frame"]) --> ARM{"Centerline avoidance weight near the car axis<br/>>= ARM_W for ARM_FRAMES consecutive frames?"}
    ARM -- no --> S
    ARM -- yes --> SNAP["Snapshot heading_ref = current heading<br/>(the straight's heading)"]
    SNAP --> CLR{"Memory places NO red/green can both far enough ahead<br/>of the axis AND close enough to the side to be in the way?<br/>held CLEAR_FRAMES frames (or 1 if a corner is imminent)"}
    CLR -- no --> HOLD["Keep dodging (pasado = 0)"]
    HOLD --> CLR
    CLR -- yes --> SKEW{"abs(heading − heading_ref) >= 25° ?"}
    SKEW -- "yes" --> FIRE["Emit pasado = 1 (one-frame pulse)<br/>trigger disarms — fires once per dodge"]
    SKEW -- "no, for GENTLE_FRAMES" --> DIS["Disarm quietly — the gentle dodge<br/>straightens itself, no RECUPERANDO"]
    FIRE --> ESP(["ESP32: SIGUIENDO → RECUPERANDO<br/>wall + gyro PID realigns the chassis"])
```

Condition 3 is what separates the two cases: same "can is now behind me" geometry, but only the crooked one triggers a recovery. The trigger disarms on fire, so it emits **once per dodge** — a can that lingers in memory while the ESP32 straightens can't re-fire it. The can positions it checks are the same `(x, y)` the memory maintains — corrected by fresh detections while the can is visible, and carried by the *same* ego-motion the centerline uses once it isn't (see the memory snippet above) — so the trigger and the path always agree on where the can is.

This replaced an earlier approach that anchored the can's position when first seen and dead-reckoned it forward with an *assumed* speed and a bicycle model; that anchor drifted 200–400 mm within 1–2 s and fired either early (nose into the can) or far too late.

### 4.5 ESP32 finite state machine (`src/ESP32/PurePursuit/PurePursuit.ino`)

```
enum Estado { SIGUIENDO, RECUPERANDO, GIRANDO, CRUCERO, MANIOBRA, TERMINANDO };
```

```mermaid
stateDiagram-v2
    [*] --> WAIT_PI: setup() blocks on READY
    WAIT_PI --> WAIT_FIRST_V2: READY acknowledged
    WAIT_FIRST_V2 --> SIGUIENDO: first V2 line (motor gated at 0 until here)

    SIGUIENDO --> RECUPERANDO: pasado=1, obstacle physically cleared [Obstacle]
    SIGUIENDO --> GIRANDO: corner detected, cooldown elapsed [Open]
    SIGUIENDO --> CRUCERO: straight clean, front sensor < FRONT_CRUCERO_CM [Obstacle]

    RECUPERANDO --> SIGUIENDO: heading settled or timeout, lane clear
    RECUPERANDO --> CRUCERO: heading settled or timeout, wall ahead [Obstacle]

    GIRANDO --> SIGUIENDO: reaches AngGiro, turn counted, heading re-zeroed
    GIRANDO --> TERMINANDO: 12th turn

    CRUCERO --> SIGUIENDO: a new "mine" obstacle appears, not yet committed
    CRUCERO --> MANIOBRA: front sensor at turn threshold (debounced), or CRUCERO timeout

    MANIOBRA --> SIGUIENDO: sub-sequence done, turn counted, new straight from 0
    MANIOBRA --> TERMINANDO: 12th turn

    TERMINANDO --> [*]: drive like SIGUIENDO for TERMINANDO_MS, then stop

    note right of MANIOBRA
      Phase machine (a motor-coast precedes every reversal — H-bridge safety):
      0 coast, 1 pivot (forward arc or reverse) to EXIT_DEG,
      2 coast, 4 straight back-off, 5 coast, then finish.
      Phase 3 = reverse stalled, coast, restart the pivot forward.
    end note
```

*This is the complete state machine as it stands on branch `SectionTurning` — the current firmware. One flag, `const bool rondaObstaculos`, selects the profile. `false` (Open Challenge): only `SIGUIENDO` / `GIRANDO` / `RECUPERANDO` / `TERMINANDO` are reachable and corners are the continuous `GIRANDO` arc. `true` (Obstacle Challenge): `GIRANDO` is replaced by the segmented `CRUCERO` → `MANIOBRA` sequence and the `pasado`-driven `RECUPERANDO` is enabled. `RECUPERANDO` never aborts on a new obstacle — it straightens the chassis first, then hands back to `SIGUIENDO`, or to `CRUCERO` if the corner is already in reach. The `main` branch still carries an earlier 3-state cut (`SIGUIENDO` / `RECUPERANDO` / `GIRANDO`); the `SectionTurning` merge is tracked as iteration log v3.0. `WAIT_PI` / `WAIT_FIRST_V2` are the startup handshake (§4.7).*

| State | Role |
|---|---|
| **SIGUIENDO** | Normal driving. In the **Obstacle round**, steering = Pi's Pure Pursuit value, blended with a light gyro correction (weight 0.12) and, only on a clean straight, the wall PID (weight 0.30). In the **Open round** the Pi's steer is ignored entirely — steering is pure wall PID + gyro PID (see §4.5.1). Watches for the next corner and for obstacle flags from the Pi. |
| **GIRANDO** | Continuous corner (**Open round only**). Servo held at full lock, motor speed ramped down in steps as `\|anguloGyro\|` grows, exits at `\|anguloGyro\| ≥ AngGiro` — **76°** in the Open round (the continuous turn coasts the rest on inertia) vs. 90° for the Obstacle round. The first corner latches the track's turn direction from whichever wall opened up. 12 corners = 3 laps → `TERMINANDO`. |
| **RECUPERANDO** | *(Obstacle round)* Entered on the Pi's `pasado=1` pulse. Vision is handed off; wall PID + gyro PID (with widened limits) straighten the chassis back into the lane. Exits when the heading error settles (with a timeout safety net for corners where one wall legitimately reads "open"). |
| **CRUCERO** | *(Obstacle round)* Straight is clean and a corner is near (front sensor < 80 cm). The car drives straight on heading toward the wall: far away, vision keeps the centerline straight; once inside `CRUCERO_GYRO_CM`, control is pure gyro + wall PID. A new obstacle sends it back to SIGUIENDO. |
| **MANIOBRA** | *(Obstacle round)* Replaces the continuous turn. At 30–60 cm from the wall a one-time decision is latched: **turn direction** = the side whose wall is open; **forward arc vs. reverse pivot** = chosen from the distance to the *outer* wall of the turn (tight against it → reverse pivot; room to swing → forward arc). A multi-phase sub-machine runs it, with motor-**coast** phases inserted between every direction reversal (plugging the H-bridge under load destroyed a TB6612 during testing). An optional short straight back-off afterward buys room on the new straight. Then it straightens, zeroes the heading for the new straight, counts the turn and returns to SIGUIENDO. |
| **TERMINANDO** | Entered automatically after the 12th turn **instead of braking on the spot**. Drives exactly like SIGUIENDO (same controller, but corner detection disabled) for `TERMINANDO_MS` (~1 s, tunable) so the car rolls forward into the start area, then cuts the motor and ends the race. Keeps the finish inside the start section instead of wherever the last corner happened to end. |

The turn-direction is latched once (all corners of a WRO track turn the same way); the forward-vs-reverse choice is made fresh at every corner from the distance to the **outer** wall of the turn ([`decidirManiobra()`](src/ESP32/PurePursuit/PurePursuit.ino)):

```cpp
// outer wall = the one that is NOT the opening (right turn → left wall, and vice-versa)
long distExt = maniobraGirarDer ? distL : distR;
maniobraReversa   = (distExt >= HUG_CM);                    // room to swing → reverse pivot
maniobraRetroceso = (distExt >  MANIOBRA_BACKOFF_MIN_CM);   // slack → short back-off after
```

**One flag switches the whole driving profile:** `const bool rondaObstaculos` at the top of `PurePursuit.ino`.

| | Open Challenge (`false`) | Obstacle Challenge (`true`) |
|---|---|---|
| Steering source | ESP32 wall PID + gyro PID **only** — the Pi's Pure Pursuit steer, `prio`/`mem`/`pasado` flags are all ignored | Pi Pure Pursuit centerline; PID as blend / fallback / RECUPERANDO |
| Corner turn | continuous `GIRANDO` | `CRUCERO` → `MANIOBRA` segmented |
| Turn target `AngGiro` | 76° (the continuous turn coasts the rest on inertia) | 90° |
| Motor PWM ceiling `MOTOR_MAX` | 180 — fast; the in-turn speed ramp does the slowing | 100 — slow, for fine maneuvers |
| `RECUPERANDO` / obstacle handling | never entered | active |

`TERMINANDO` and the cascade PID run in both.

#### 4.5.1 Open-round corner hardening

With the Pi's vision out of the loop, three guards keep the continuous turn honest:

- **`giroArmado` — corridor arm.** `detectarEsquina()` is not allowed to fire a turn until the car has first confirmed it is *inside* a corridor: both side walls < 100 cm for `PASILLO_FRAMES` (3) consecutive frames. A wide reading in the start zone therefore can't trigger a false first turn. Once armed it stays armed for the whole run, so real corners are never delayed by it (unlike a fixed time lockout).
- **Front-wall approach slow-down.** When the front sensor sees the end wall closer than `FRONT_SLOWDOWN_CM` (60 cm), speed drops to `VEL_APROX_CERRADA` (140) so `detectarEsquina()` gets a clean read of which side opens before the car is on top of the corner.
- **`marchaIniciada` timer re-anchor.** The start-guard timer (`timeStart`) is reset to the instant the car actually starts rolling — not to when `READY` arrived seconds earlier — so its window is measured from roll-off.

### 4.6 Cascade PID (always running underneath)

Even in Pure Pursuit mode the ESP32 computes its dual cascade PID every loop — it is the fallback, the RECUPERANDO/CRUCERO controller, and the blend term in SIGUIENDO.

```
                ┌────────────────────┐   heading    ┌────────────────────┐
  distL─distR ─►│     OUTER PID      │─ setpoint ──►│     INNER PID      │──► servo
                │   (wall centering) │              │  (heading control) │
                └────────────────────┘              └────────────────────┘
                         ▲                                    ▲
                  HC-SR04 readings                    MPU-6050 heading
```

The single-loop `error = distL − distR` controller it replaced failed past ~30° of yaw: the HC-SR04's conical beam hits the wall obliquely, both sensors over-report, the difference sits near zero while the car drifts into a wall. The outer loop turns lateral wall error into a target heading; the inner loop drives the servo to that heading using the IMU, which doesn't care about beam geometry.

**Tuned gains:** `KpWall 1.0 / KiWall 0.0 / KdWall 1.2`, `KpGyro 2.0 / KiGyro 0.0 / KdGyro 0.5`. Both integral terms are **disabled on purpose** — integral built up on long straights and released as a large steering impulse at corner entry, overshooting into the opposite wall. The derivative terms give enough steady-state correction on their own. Raw ultrasonic reads pass through an EMA filter (`alpha = 0.85`) before the PID.

```cpp
// OUTER: lateral wall error → steering contribution (Ki = 0)
errorWall  = constrain(distL - distR, -50, 50);
outputWall = KpWall*errorWall + KdWall*(errorWall - prevErrorWall)/dt;

// INNER: heading error vs. the straight's reference heading (Ki = 0)
errorGyro  = anguloObjetivo - anguloGyro;
outputGyro = KpGyro*errorGyro + KdGyro*(errorGyro - prevErrorGyro)/dt;

// SIGUIENDO with Pure Pursuit active: the Pi's steer leads, PID only trims a clean straight
servo = centroServo - (steerDeg - outputGyro*PP_GYRO_BLEND - outputWall*PP_WALL_BLEND);
// fallback / RECUPERANDO / CRUCERO-near-wall: PID alone
// servo = centroServo + (outputWall + outputGyro);
```

Heading is integrated on the ESP32 from the gyro Z axis, with the 1°/s deadband that keeps MEMS thermal noise from drifting the straight-line heading:

```cpp
float gz = mpu.getGyroZ() / gyroScale;
if (abs(gz) < 1.0) gz = 0;        // 1°/s deadband
anguloGyro += gz * dt;            // this is the value echoed back to the Pi
```

### 4.7 Startup handshake

1. Pi lights the LED on **GPIO 27** — "Pi is up".
2. Pi waits for the start button on **GPIO 17**.
3. Camera warm-up (~40 frames discarded to settle exposure).
4. Pi sends `READY` ×3; the ESP32 has been blocking in `setup()` waiting for it.
5. ESP32 replies `ACK:READY`, then **holds the motor at zero until the first real V2 line arrives** (a gate so the car never rolls forward on the fallback PID before Pure Pursuit is actually streaming). On the first frame it then rolls, `marchaIniciada` re-anchors the start-guard timer to that instant.
6. Main loop runs until 12 turns are counted, then `TERMINANDO` drives ~1 s more into the start area and stops.

```mermaid
sequenceDiagram
    participant Pi as Raspberry Pi
    participant ESP as ESP32
    Pi->>Pi: Light LED on GPIO 27 ("Pi is up")
    Pi->>Pi: Wait for start button (GPIO 17)
    Pi->>Pi: Camera warm-up (~40 frames discarded)
    Note over ESP: setup() is blocking, waiting for READY
    Pi->>ESP: READY x3
    ESP->>Pi: ACK:READY
    Note over ESP: Motor held at 0 until the first V2 line
    Pi->>ESP: First V2 line (obs + flags)
    Note over ESP: Car rolls — start-guard timer re-anchored to this instant
    loop Every processed frame (~12-15 Hz)
        Pi->>ESP: V2 line — obs, prio, mem, pp, pasado
        ESP->>Pi: ACK:V2 — ang (heading), est (S/G/R), dir (?/L/R)
    end
    Note over ESP: 12 turns counted, then roll ~1 s into start zone and stop
```

### 4.8 Development status

| Module | Challenge | Status |
|---|---|---|
| BEV homography + 9-point calibration tool | both | Complete |
| Floor centerline extraction | both | Complete |
| Pure Pursuit geometric controller | both | Complete, track-tuned |
| ESP32 cascade PID + fallback | both | Complete |
| Continuous corner turn (GIRANDO) | Open | Complete, track-tuned |
| Open-round pure-PID mode + corner hardening (`giroArmado`, approach slow-down) | Open | Implemented, not track-tuned |
| Return-to-start finish (TERMINANDO) | both | Implemented, not track-tuned |
| Pillar detection (HSV + shape filter) | Obstacle | Complete |
| Asymmetric WRO keep-out in centerline | Obstacle | Complete |
| Rolling obstacle memory (dead reckoning) | Obstacle | Complete, track-tuned |
| Corner-line "mine / beyond" classifier | Obstacle | Complete |
| Measured-state RECUPERANDO trigger | Obstacle | Complete, track-tuned |
| Segmented turn (CRUCERO → MANIOBRA) | Obstacle | Implemented, tuning on track |
| Mid-turn cone detector | Obstacle | Phase 1 — logging only |
| Parking maneuver | Obstacle | In development |

---

# 5. Systemic Thinking & Engineering Decisions

### 5.1 Subsystem interaction map

```mermaid
flowchart LR
    subgraph PI["Raspberry Pi 4 — vision and planning"]
        CAM["Pi camera"] --> BEV["BEV homography"]
        BEV --> PD["Pillar detection (HSV)"]
        BEV --> CL["Centerline<br/>asymmetric keep-out"]
        PD --> OM["Rolling obstacle memory"]
        OM --> CL
        OM --> TRG["RECUPERANDO trigger"]
        CL --> PP["Pure Pursuit"]
    end
    subgraph ESP["ESP32 — real-time control"]
        OUT["OUTER PID<br/>wall centering"] --> INN["INNER PID<br/>heading via IMU"]
        FSM["Finite state machine"]
        SEG["CRUCERO / MANIOBRA<br/>segmented turn"]
        INN --> ACT(["servo + motor PWM"])
        FSM --> ACT
        SEG --> ACT
    end
    USLR["HC-SR04 left / right"] --> OUT
    USF["HC-SR04 front"] --> SEG
    IMU["MPU-6050"] --> INN
    PP -- "obs (V2 @ 115200)" --> FSM
    TRG -- "prio / mem / pasado" --> FSM
    IMU -- "ACK: heading" --> OM
```

The IMU heading is the shared currency: the ESP32 integrates it for its own control *and* ships it back so the Pi's obstacle memory can rotate its map by the exact same angle. Everything the Pi decides reaches the ESP32 as four flags and one number; everything the ESP32 knows about its own state reaches the Pi as three fields. Neither side can stall the other.

### 5.2 Key engineering trade-offs

**Trade-off 1 — one processor vs. two.** One ESP32 would remove the UART protocol, the Linux boot time and the sync logic. But real-time computer vision breaks single-core timing: a 640 × 480 HSV pass is 8–15 ms on the Pi 4, and running it alongside µs-accurate GPIO pulses gives non-deterministic jitter. Splitting by hardware strength (Pi = vision + planning, ESP32 = timing + actuation) lets each run at its own rate; a delayed packet just means the ESP32 reuses the last command. The cost — a protocol to maintain and two codebases — was worth deterministic control.

**Trade-off 2 — VL53L0X ToF vs. HC-SR04 ultrasonic.** ToF wins on paper (±3 mm vs ±15 mm, narrow beam). But the WRO field's matte-black walls absorbed the 940 nm IR and returned out-of-range at 300 mm in our tests. Ultrasonic reflects off anything. We chose reliability and closed the accuracy gap with EMA filtering, a front-channel median filter, and the cascade PID.

**Trade-off 3 — reactive steering vs. geometric Pure Pursuit.** The first vision controller steered proportionally to the pillar's pixel offset. It over-reacted close in and under-reacted far out, and had no model of the car's path. Pure Pursuit against a BEV centerline gives a geometrically correct steering angle for a chosen look-ahead, and the look-ahead becomes a single tuning knob for "how hard to dodge". The cost is the BEV calibration step; the payoff is predictable arcs instead of hand-tuned reaction curves.

**Trade-off 4 — forgetting a can when it leaves the frame vs. a rolling memory.** The honest, stateless option is to only avoid what the camera sees now — but that cuts the corner onto a can the moment it drops out of view. The rolling memory keeps the keep-out alive using dead reckoning (assumed speed + real IMU rotation). The risk it adds — a "ghost" can from accumulated error — is bounded by confidence decay and a prune-on-pass rule, and is the safer failure (dodge a can that's already gone vs. clip one that's still there).

**Trade-off 5 — continuous turn vs. segmented stop-and-maneuver (Obstacle round).** A continuous 90° arc is fast and simple and works well in the Open round. In the Obstacle round, a can placed near the corner mouth turns that blind arc into a coin-flip. The `SectionTurning` design trades speed for certainty: cruise straight to a known distance from the wall (front sensor), stop, then run a deterministic maneuver — a forward arc if there's room, a reverse pivot if the car is tight against the outer wall. It is slower, but every corner becomes repeatable, which is the same principle that drove the 100:1 gear choice.

**Trade-off 6 — forward arc vs. reverse pivot inside MANIOBRA.** A forward arc needs clear space ahead to swing through; a reverse pivot needs the car close to the wall first. Rather than pick one, the firmware measures the distance to the outer wall of the turn and chooses per corner, with a reverse-timeout that bails out into a forward finish if the pivot stalls.

### 5.3 Iteration log

Structural changes and the tuning passes that revealed something — routine per-run parameter tuning in `config.py` between track sessions is not listed. Each row links to the commit that introduced the change. `Status`: **Shipped** (on `main`, track-validated) · **On branch** (implemented, still tuning) · **Superseded** (replaced by a later row) · **Reverted** (tried on track, backed out).

A dated, phase-by-phase account of the same history — including the pre-repo design and per-peripheral bring-up work — is in the [Engineering Journal](ENGINEERING_JOURNAL.md).

| Stage | Date | Change | Why it changed | Evidence | Status |
|---|---|---|---|---|---|
| Mechanical + PCB | 2026-04-13 → 04-24 | Chassis, rack-and-pinion steering, printed differential and power PCB, designed from scratch | New vehicle every season | `283078e` … `51ea239` | Shipped |
| First firmware | 2026-05-09 | Single-loop PID on `distL − distR`, VL53L0X ToF ×2, 3-state FSM (`Controller_PI.ino`) | First open-round lap | `61544cb` | Superseded |
| v1.1 — ToF → ultrasonic | 2026-05 | Both VL53L0X replaced with HC-SR04 | ToF lost the black wall past ~70 cm — [ERR-01](#err-01--vl53l0x-lost-the-black-wall-past-70-cm) | `61544cb` era | Shipped |
| v1.2 — remove the integrators | 2026-05 → 06 | `Ki = 0` on both PID loops | Integral wound up on the straights and released as one impulse at corner entry → overshoot into the far wall | `Controller_PI.ino` history | Shipped |
| v1.3 — cascade PID | 2026-05 → 06 | Outer loop (wall error → target heading) + inner loop (heading → servo, via IMU) | The `distL − distR` error goes blind past ~30° of yaw — [ERR-02](#err-02--wall-error-goes-blind-at-high-yaw) | `Controller_PI.ino` history | Shipped |
| Camera integration | 2026-05-23 | Pi camera, track-edge detection, BEV calibration tool (`calibrate.py`) | Lane geometry the ultrasonics can't see | `21fe8df`, `5797487` | Superseded |
| Two-controller split + deploy infra | 2026-06-08 → 06-09 | Pi ↔ ESP32 over UART; `wro-runtime.service`, VNC, push-to-deploy CI | OpenCV latency and µs GPIO timing can't share one core ([§5.2](#52-key-engineering-trade-offs)) | `69f82a9`, `a065d78` | Shipped |
| v2.0 — Pure Pursuit + centerline | 2026-06-13 → 06-22 | BEV homography → floor centerline → geometric Pure Pursuit (`pure_pursuit/`) | Reactive pillar-offset PID had no path model — over-reacted near, under-reacted far | `95f3744`, `e494d8c`, `556266b` | Shipped |
| Camera lens FOV 63° → 120° | 2026-07 → 08-07 | Wide-angle NoIR lens (swapped over the July break); on return, pinned white-balance (`awb-enable=false colour-gains=<1.2,1.5>`) and re-tuned the obstacle RGB ranges | Needed more forward range for the obstacle round; the wide lens has no IR-cut filter, so the raw image had a heavy red cast — [ERR-03](#err-03--wide-angle-noir-lens-put-a-red-cast-on-every-frame) | `945c2f1` | Shipped |
| v2.1 — offline sim | 2026-08-11 | Kinematic bicycle sim (`pure_pursuit_sim.py`, 520 lines) + `runtime_nuevo.py` | Tune controller logic without track time | `0a2c5d2` | Shipped |
| v2.2 — BEV calibration 4 → 9 points | 2026-08-13 | RANSAC fit over a 3×3 marker grid | A 4-point fit is exact — no way to reject a mis-click or check reprojection error | `daf1e03` | Shipped |
| v2.3 — corner-line detection | 2026-08-17 → 08-19 | Orange / blue ground-line tracking in the BEV | Turn trigger + a "my straight vs. the next one" boundary for obstacles | `d3a611e`, `8edc1b8` | Shipped |
| v2.4 — wall-aware steering (`ParedCenterline`) | 2026-08-20 → 08-21 | Centerline biased by ultrasonic wall distance; V2 protocol fixes | Centerline alone drifted toward the outer wall on wide corners | merges `f5066e1`, `24b2ec7` | Shipped |
| Open round validated | 2026-08-28 | — | 10 complete autonomous runs from varied start positions and field configs → focus moved to the Obstacle Challenge | [§6.2](#62-results-to-date) | Shipped |
| v2.5 — rolling obstacle memory | 2026-08-24 → 08-27 | Seen cans kept in a robot-relative map, advanced by assumed speed + **real IMU heading** from the ACK | Can leaves the frame → keep-out vanishes → centerline cuts the corner onto it | `a41ac0e`, `3c96abf`, `57d3218` | Shipped |
| v2.6 — hot start + run recording | 2026-08-28 | Pipeline runs disarmed during the button delay; ESP32 gated on the first V2 line; MJPG `.avi` HUD capture from button-press | Cold camera/serial cost ~2 s at the start; every run now leaves a reviewable artifact | `3245c1c`, `2355caf`, `f257371` | Shipped |
| v2.7 — undervoltage fix → frame-rate rescale | 2026-08-28 | Re-fed the Pi through 22 AWG leads (was dropping 0.3 V PCB→Pi → brown-outs, garbled frames); loop went ~7 → ~14 Hz; re-scaled every per-frame knob (slew, recovery frames, look-ahead floor) | Half the tunables were calibrated at 7 Hz and were now firing twice as fast — [ERR-08](#err-08--raspberry-pi-undervoltage-from-undersized-power-wiring) | `e4ca4f9`, `1a19cdb` | Shipped |
| v2.8 — pivot-trap root cause | 2026-08-28 → 08-29 | `LOOKAHEAD_MIN_PX` 60 → 78 (60 saturated the PP geometry); adaptive look-ahead + steer-gain re-keyed on the **longitudinal** gap; `forget_color_obstacles()` on pass so the centerline un-bends | Near a can the steer term hit ±0.9 (≈ full lock) → the car pivoted in place instead of arcing; `y` never advanced, RECUPERANDO never armed — [ERR-06](#err-06--the-car-pivoted-in-place-instead-of-arcing) | `1daf563` | Shipped |
| v2.9 — RECUPERANDO: anchor → measured state | 2026-08-28 → 08-29 | Retired the geometric dead-reckoning anchor; the trigger now reads the centerline avoidance weight, a heading snapshot, and the memory's own "is a can still in the way" test (`ARM` / `CLEAR` / `SKEW`) | The anchor integrated an *assumed* linear speed and drifted 200–400 mm in 1–2 s whenever the car had to turn hard — [ERR-07](#err-07--recuperando-trigger-tied-to-assumed-linear-speed) | `f24c547` → `25d0565` → **`52549c8`** | Shipped |
| v2.10 — turn-direction from the orange line | 2026-08-31 | Direction latched from the orange corner-line slope **during the run**, not pre-set | A pre-set direction is one more thing to get wrong at check-in | `a72a751`, `e641817` | Shipped |
| v2.11 — exterior cone at the corner mouth | 2026-08-31 | A can right at the corner: drive straight past it, *then* turn | The blind turn arc would sweep into it | `4e5ca40` | Shipped |
| v2.12 — camera-safe service restart | 2026-08-31 | CI + ops use `stop → sleep 4 → start`, never `systemctl restart` | `restart` doesn't release the CSI device — camera wedges, LED stays dark | `9aff6c9` | Shipped |
| v3.0 — segmented turns (`SectionTurning`) | 2026-09-01 | Obstacle round only: `GIRANDO` → `CRUCERO` (cruise to a set distance on the front sensor) → `MANIOBRA` (forward arc **or** reverse pivot from outer-wall distance); motor-coast phase before every direction reversal | A can at the corner mouth makes a blind 90° arc a coin-flip; a missing coast delay had already killed a driver + a motor — [ERR-04](#err-04--tb6612-and-motor-destroyed-by-a-reversal-with-no-coast-delay) | `9219f17` (+386 lines to `.ino`) | On branch |
| v3.1 — mid-turn cone detector | 2026-08-31 | `mid_turn.py` — raw per-frame BEV projections (rolling memory is off during a pivot); **Phase 1: log only** | A can first seen *during* the turn ends up beside the car afterwards → clipped | `6b0b5c7` | On branch (logging) |
| v3.2 — Open round runs pure PID | 2026-09-03 → 09-04 | Open round ignores the Pi steer — wall + gyro PID only; per-round `AngGiro` / `MOTOR_MAX`; `giroArmado` corridor-arm; front-wall approach slow-down; `TERMINANDO` finish | Open round doesn't need vision and was inheriting obstacle-round speed caps; a wide start-zone reading latched a false first turn — [ERR-05](#err-05--ultrasonic-beam-cone-bounces-off-the-corner) | `626fc91`, `13e05c1` | On branch |

### 5.4 Risk analysis

| Risk | Likelihood | Impact | Mitigation |
|---|---|---|---|
| HC-SR04 spike reading | Medium | Medium — brief PID disturbance | EMA on all channels; 5-sample median on the front channel; cascade inner loop dampens |
| Gyro drift over 3 laps | Low | Medium — heading offset grows | 1°/s deadband; heading zeroed after every turn; startup bias calibration |
| Camera mount shifts after BEV calibration | Low | High — warped top-view, wrong centerline | Rigid printed camera frame; recalibrate if the mount is touched; reprojection-error check in `calibrate.py` |
| Can leaves FOV mid-dodge → ghost obstacle | Medium | Medium — phantom keep-out | Confidence decay; prune-on-pass; memory disabled during turns |
| UART packet delayed by OpenCV load | Medium | Low — one stale command | ESP32 reuses last command; 800 ms timeout → autonomous wall+gyro fallback |
| Corner missed / mis-counted | Low | High — wrong lap count or direction | Conservative thresholds; 2 s cool-down; `prio`/`mem` block detection while dodging; front-sensor debounce in the Obstacle round |
| False first turn from a wide start-zone reading (Open round) | Medium | High — wrong direction latched for the whole run | `giroArmado`: corner detection stays disabled until both walls read < 100 cm for 3 frames; timers re-anchored to roll-off |
| MANIOBRA runs the car into the outer wall | Medium | High — DQ | Forward/reverse chosen from measured outer-wall distance; reverse-timeout fallback; optional post-maneuver back-off |
| H-bridge damage from direction reversal under load | Low (mitigated) | High — dead driver | Motor-coast phase inserted before every direction change (learned the hard way) |
| Servo driven into its end stop | Low | Low | Firmware clamps servo command to 20°–150° |

### 5.5 Failure & Incident log

Post-mortems for the failures that changed the design — what happened, the confirmed or suspected root cause, and what shipped in response. Several of these are the "learned the hard way" behind a row of the risk table in [§5.4](#54-risk-analysis).

#### ERR-01 — VL53L0X lost the black wall past 70 cm

| | |
|---|---|
| **First seen** | 2026-05, first wall-following bring-up |
| **Setup** | Two VL53L0X, one per side — the same left/right wall-distance job the HC-SR04s do now. |
| **Symptom** | Against the matte-black outer wall the effective range collapsed: past ~70 cm the sensor stopped returning correct distances. White walls read to spec. |
| **Impact** | No usable lateral reference on the black-walled portions of the track — roughly half the perimeter. |
| **Root cause** | The 940 nm IR is absorbed by the matte-black surface; too little returns for a time-of-flight solve. A single sensor on the bench reproduced it, so not a wiring or I²C fault. |
| **Fix** | Switched both channels to HC-SR04 ultrasonic (`61544cb` era) — sound reflects off any surface regardless of colour. Traded ±3 mm for ±15 mm and closed the gap in software (EMA on all channels, a 5-sample median on the front channel, the cascade PID). |
| **Status** | Resolved. Trade-off in [§5.2](#52-key-engineering-trade-offs). |

#### ERR-02 — wall error goes blind at high yaw

| | |
|---|---|
| **First seen** | 2026-05 — one of the earliest problems, open-round bring-up |
| **Symptom** | On corner entry and recovery the car kept drifting into a wall even though the PID output stayed small and stable. |
| **Root cause** | The HC-SR04's ~15° beam cone hits the wall obliquely once the chassis is yawed; both sensors over-report by similar amounts, so `distL − distR` sits near zero while the car is visibly crabbing toward one wall. This is inherent to the sensor geometry and is **still true today**. |
| **Fix** | The cascade PID stops the car *acting* on the blind error: the **outer** loop turns lateral wall error into a target heading, the **inner** loop drives the servo to that heading from the **IMU** ([§4.6](#46-cascade-pid-always-running-underneath)). At high yaw the wall term is unreliable but the inner loop is still steering on a good heading signal, so the car tracks true and re-centres once the walls read cleanly again. |
| **Status** | Mitigated by design — the sensor limitation remains; the IMU inner loop is what keeps it from mattering. This cascade is also the fallback / RECUPERANDO / CRUCERO law and the blend term in SIGUIENDO. |

#### ERR-03 — wide-angle NoIR lens put a red cast on every frame

| | |
|---|---|
| **First seen** | 2026-07, after the lens swap; corrected on return, 2026-08-07 |
| **Change that caused it** | Moved from a ~63° lens to a ~120° wide-angle lens to see far enough ahead to react to a pillar and read the corner on the same frame. The wide lens has no IR-cut filter (NoIR). |
| **Symptom** | Every frame came out heavily red-tinted. HSV masks for the floor, the orange line and the red/green pillars all broke. |
| **Root cause** | With no IR-cut filter the sensor integrates near-IR the eye doesn't see; on this sensor it lands mostly in the red channel. |
| **Fix** | Pinned the libcamera pipeline to fixed white-balance — `libcamerasrc awb-enable=false colour-gains=<1.2,1.5>` — so auto-WB can't chase the cast, then re-tuned the red/green HSV ranges on the corrected image (`945c2f1`, 2026-08-07, and the `vision.py` range passes after it). |
| **Status** | Resolved. The wide FOV is now a net win — more track and obstacle zone per frame. |

#### ERR-04 — TB6612 and motor destroyed by a reversal with no coast delay

| | |
|---|---|
| **First seen** | 2026-08 → 09, `SectionTurning` MANIOBRA bring-up |
| **Symptom** | While testing the maneuver, the code switched the motor from forward to reverse with no gap between the two. A current spike followed; **one TB6612 driver and one N20 motor were lost.** |
| **Root cause** | Software, not hardware: the forward → reverse transition energised the H-bridge in the opposite direction while the motor was still spinning. Back-EMF plus shoot-through current during the flip exceeded the driver's rating (classic "plugging"). |
| **Fix** | Every direction change in the firmware — forward↔reverse, in MANIOBRA and everywhere else — now passes through a mandatory motor-coast phase (`A1 = A2 = LOW`, `MANIOBRA_FRENO_MS = 300`) so the motor spins down before the opposite direction is energised (`9219f17`). |
| **Status** | Resolved. No recurrence since the coast phase went in. Risk table: "H-bridge damage from direction reversal under load". |

#### ERR-05 — ultrasonic beam cone bounces off the corner

| | |
|---|---|
| **First seen** | 2026-08, open-round corner tuning |
| **Symptom** | The car would sail past a corner opening — it "thought" it had not reached the end wall yet when it had actually passed the turn point some time earlier. |
| **Root cause** | The front HC-SR04's beam cone widens with distance; far from the end wall it catches the *corner* geometry and returns a longer bounce path, so the front distance reads larger than the true straight-ahead gap. Corner detection kept waiting. |
| **Fix** | The car slows to `VEL_APROX_CERRADA` once the front sensor drops below `FRONT_SLOWDOWN_CM` (60 cm) — more time to read *which* side opens before it is on top of the corner. Plus EMA + a 5-sample front-channel median to reject spikes, and a multi-frame confirmation before a turn is accepted. In the Obstacle round the same read drives `CRUCERO → MANIOBRA` instead of a continuous arc. |
| **Verification** | 10 complete open-round runs from varied start positions and field configurations after these changes. |
| **Status** | Resolved. |

#### ERR-06 — the car pivoted in place instead of arcing

| | |
|---|---|
| **First seen** | 2026-08-28, sessions ~orillas 414–416, right after the frame-rate doubled ([ERR-08](#err-08--raspberry-pi-undervoltage-from-undersized-power-wiring)) |
| **Symptom** | Approaching a can, the car rotated on the spot instead of driving a curve around it. The can's `y` in the BEV barely moved (≈ 40 mm/s) — turning, not translating. RECUPERANDO then never fired (the memory never saw the can go behind the axis) so the car dug deeper in. |
| **Root cause** | (1) the obstacle steer term jumped to ±0.9 — near full lock — which pivots this chassis at cruise PWM; (2) `LOOKAHEAD_MIN_PX = 60` saturated the Pure Pursuit geometry, and the adaptive look-ahead / steer-gain keyed on **Euclidean** distance, so a can level with the car but off to the side kept those relaxed and the car drove past the point it should have turned. |
| **Fix** | `LOOKAHEAD_MIN_PX` 60 → 78; adaptive look-ahead (100 → 78 px) and `_distance_steer_gain` (0.30 → 1.0) re-keyed on the **longitudinal** gap; on a confirmed pass the runtime calls `memory.forget_color_obstacles()` so the centerline un-bends and the car eases out (`1daf563`). |
| **Verification** | Session orillas 417: dodge steer ±0.4–0.7, the can's `y` advanced through the pass = arc not pivot, both cans cleared, all 12 turns completed. |
| **Status** | Resolved. |

#### ERR-07 — RECUPERANDO trigger tied to assumed linear speed

| | |
|---|---|
| **First seen** | 2026-08-28, on-track (`f24c547` geom v1, `25d0565` geom v2) |
| **Symptom** | The recover-into-lane state fired either too early — nosing into the can it was meant to have cleared — or seconds too late, after the car had already straightened badly. Worst whenever the pass needed a large heading change. |
| **Root cause** | The trigger anchored the can's position when first seen and dead-reckoned it forward using an **assumed linear speed** through a bicycle model. With no measurement feedback the anchor drifted 200–400 mm in 1–2 s, and a hard dodge — car rotating, barely translating — broke the speed assumption entirely. `SPEED_SCALE` at 1.0 / 0.35 / 0.60 were all wrong somewhere. |
| **Fix** | Retired the anchor (`52549c8`). `_measured_recup_trigger` reads state that is already measured: **ARM** when the centerline's avoidance weight near the axis has been high for several frames (snapshot the heading), **CLEAR** when the rolling memory places no can in the path, fire only if **SKEW** — `|heading − snapshot| ≥ 25°`. A gentle dodge that straightens itself never stops for a recovery. |
| **Status** | Resolved. Finding a dodge shape that armed RECUPERANDO *reliably* was the single longest debugging effort of the obstacle round. Full history in [§4.4](#44-obstacle-handling-obstacle-challenge). |

#### ERR-08 — Raspberry Pi undervoltage from undersized power wiring

| | |
|---|---|
| **First seen** | 2026-08 |
| **Symptom** | Frames processed poorly or not at all; the Pi would sometimes power off mid-run. Intermittent, load-dependent. |
| **Root cause** | ~0.3 V drop between the PCB 5 V rail and the Pi's input on undersized power leads. Under vision + steering load the Pi input sagged below its undervoltage threshold and it throttled or browned out. |
| **Fix** | Re-ran the Pi feed in 22 AWG. The rail held; the processing loop went from ~7 fps to ~14 fps. |
| **Follow-on** | The frame-rate jump then destabilised the evasion tuning — several knobs were expressed per-frame, and doubling the rate doubled their effect. Every per-frame parameter was re-scaled (iteration log v2.7); the pivot-trap ([ERR-06](#err-06--the-car-pivoted-in-place-instead-of-arcing)) surfaced in the same window. |
| **Status** | Resolved (wiring). Pi input voltage is now on the pre-run checklist. |

#### ERR-09 — separating "my straight" from "the next straight" *(open)*

| | |
|---|---|
| **First seen** | 2026-09, `SectionTurning` |
| **Symptom** | A can on the *next* straight, visible over the corner, is sometimes treated as an obstacle on the current straight (or vice-versa). Wrong classification → an unnecessary dodge, or a real can ignored. |
| **Current handling** | `corner_lines.py` tracks the orange corner line row-by-row in the BEV and labels each remembered can *mine* / *beyond* with asymmetric hysteresis (quick to start avoiding, slow to stop). Tried and reverted: locking onto the primary can by camera-bbox height (`601ea8d` … `ad4f71e`, 2026-09-02 — bbox too noisy frame to frame). |
| **Impact** | The main reason the obstacle round is not yet complete on every field configuration. Simple layouts pass reliably; a can straddling the corner sightline does not. |
| **Status** | **Open — active work.** |

---

# 6. Testing & Validation

### 6.1 How we test

Almost all tuning is done from **recorded track runs**. The runtime writes a combined camera + bird's-eye-view HUD to an MJPG `.avi` from the moment the start button is pressed, with the decision journal burned in (`[DET]` detections, `[MTURN]` mid-turn detector, `[RECUParm]` recovery arm-state, `[PPDIAG]` Pure Pursuit diagnostics); `journalctl -u wro-runtime.service` captures the same lines on the Pi. Sessions are numbered sequentially (`orillasNNN`) — the counter has incremented on every integrated run since the Pi ↔ ESP32 link came up in June 2026 and is now around **700**. The loop is: run on track → review HUD + log → change **one** thing → re-run the same configuration.

| Tool | Scope | Runs without |
|---|---|---|
| `pure_pursuit/pure_pursuit_sim.py` | Kinematic bicycle sim of centerline + Pure Pursuit + obstacle-memory logic | car, track |
| `pure_pursuit/test_vision.py` | HSV masks, pillar shape filter, BEV warp — live camera or a recorded clip | ESP32, motors |
| `src/RASPI/tests/` | UART framing diagnostics, kinematic simulation | car |
| `src/ESP32/TestCodes/` | Per-peripheral bring-up — servo sweep, gyro read, motor direction, ultrasonic ping, serial echo | full firmware |

### 6.2 Results to date

**Open Challenge — validated.** After the corner-detection work ([ERR-05](#err-05--ultrasonic-beam-cone-bounces-off-the-corner)): **10 complete autonomous runs** from varied start positions and field configurations, no wall contact, correct finish. Three laps in ~12 s at 60 % motor speed. Reference run: [YouTube](https://youtu.be/orP-BNSG-6s).

**Obstacle Challenge — in progress.** Simple layouts: the car completes the round comfortably. Layouts with a can straddling the corner sightline still fail on the *mine vs. beyond* classification ([ERR-09](#err-09--separating-my-straight-from-the-next-straight-open)) — the current blocker. The pivot-trap fix ([ERR-06](#err-06--the-car-pivoted-in-place-instead-of-arcing)) was confirmed clean at orillas 417 (both cans cleared, 12 turns). Segmented turns (`CRUCERO → MANIOBRA`) are being tuned on track. The parking maneuver is **not yet designed** — full obstacle-round completion comes first.

### 6.3 Validation matrix

Figures are from our own test runs and recorded HUD footage, not lab instrumentation — treat them as working estimates.

| # | Quantity | Method | Result |
|---|---|---|---|
| 1 | End-to-end Open pass rate | Clean runs / attempts, varied start + config | 10 documented clean; total attempt count not logged |
| 2 | Open lap time | Stopwatch, 3 laps at 60 % motor | ~12 s |
| 3 | Obstacle round, simple layouts | Clean runs / attempts | Passes reliably — exact ratio not logged |
| 4 | Obstacle round, can across the corner sightline | Clean runs / attempts | Fails — see [ERR-09](#err-09--separating-my-straight-from-the-next-straight-open) |
| 5 | Pivot-trap fix | Dodge-steer amplitude + can `y` progression, recorded | orillas 417: steer ±0.4–0.7, `y` advances = arc |
| 6 | Gyro heading total over a full run | Integrated rotation vs. the 1080° geometric total (12 × 90°), one measured run | ~1010° vs. 1080° — ≈ 6.5 % low. Does not accumulate: heading is zeroed at every turn and the wall + centerline correction on each straight absorbs the residual |
| 7 | BEV projection accuracy | Marker position in the warped view vs. its real floor position, inside the calibrated area | ≈ ±5 cm within the calibrated area |
| 8 | Minimum turning radius | Full-lock circle at competition speed | ≈ 18 cm (approx.; not measured separately left/right) |
| 9 | MANIOBRA forward-vs-reverse decision | `decidirManiobra()` choice vs. what the corner needed | No wrong choice in recent testing (weeks of runs) |
| 10 | RECUPERANDO trigger accuracy | Per recorded dodge: fired only when the chassis was actually crooked | No mis-fire in recent sessions since the measured-state trigger ([ERR-07](#err-07--recuperando-trigger-tied-to-assumed-linear-speed)); systematic count still pending |
| 11 | Pillar colour classification | Recorded runs under venue-like light, red/green confusion count | No known misclassifications after the white-balance fix ([ERR-03](#err-03--wide-angle-noir-lens-put-a-red-cast-on-every-frame)); earlier colour-ID bugs resolved |

### 6.4 Pre-run checklist (each venue)

1. Camera warm-up — ~40 discard frames, stable exposure.
2. BEV homography — recalibrate if the mount was touched; check the reprojection residual from `calibrate.py`.
3. HSV ranges — re-tune floor / orange line in `config.py` and red / green pillars in `vision.py` for the venue lighting (auto-WB / auto-gain stay off).
4. Vision-only sanity check — `python -m pure_pursuit.test_vision`, no ESP32, no motors.
5. Firmware — `rondaObstaculos` set for the round; correct build flashed.
6. Pi input voltage checked **at the Pi**, not just at the PCB ([ERR-08](#err-08--raspberry-pi-undervoltage-from-undersized-power-wiring)); battery voltage logged; `journalctl` clean at idle.
7. Start-up handshake — LED on GPIO 27 lights, button on GPIO 17 responds, `ACK:READY` seen.

### 6.5 Milestones

The project arc, oldest first. Full acceptance criteria follow for the milestones that decide competition results and are not yet fully validated (M8–M11). `Status`: **Completed** · **Partially validated** (bar met in testing, evidence not fully logged) · **Under test** · **In progress** · **Not started**.

The [Engineering Journal](ENGINEERING_JOURNAL.md) places these milestones on the dated build timeline, alongside the work between them.

| # | Milestone | Date | Status |
|---|---|---|---|
| M1 | Functional, structurally stable chassis that integrates every component | 2026-04 | Completed |
| M2 | Per-peripheral test sketches — each ultrasonic, the servo and the DC motor bench-tested in isolation ([`src/ESP32/TestCodes/`](src/ESP32/TestCodes/)) | 2026-05 | Completed |
| M3 | Base wiring / circuit design, validated on a breadboard | 2026-04 | Completed |
| M4 | Custom PCB laid out to fit the finished mechanical model and free up space in the vehicle ([§3.3](#33-pcb--wiring)) | 2026-04 → 05 | Completed |
| M5 | First integrated firmware — every peripheral driven from one control loop | 2026-05 | Completed |
| M6 | Raspberry Pi ↔ ESP32 link — V2 line protocol, deploy service, live view ([§4.2](#42-inter-controller-protocol-v2)) | 2026-06 | Completed |
| M7 | Colour sensing wired to steering **and** throttle — the car reacts to a pillar (red/green detection prototyped 2026-05/06; integrated and tested on-track 2026-08) | 2026-06 → 08 | Completed |
| M8 | Open Challenge, full autonomous run — see [MIL-01](#mil-01--open-challenge-full-autonomous-run) | 2026-08-28 | Partially validated |
| M9 | Efficient obstacle-avoidance algorithm — see [MIL-02](#mil-02--obstacle-avoidance-standard-layouts) | 2026-08 → 09 | Under test |
| M10 | Every obstacle-round layout covered — see [MIL-03](#mil-03--obstacle-challenge-full-layout-coverage) | — | In progress |
| M11 | Parking inside the bay — see [MIL-04](#mil-04--parking-maneuver) | — | Not started |

#### MIL-01 — Open Challenge, full autonomous run

| | |
|---|---|
| **Objective** | Complete the Open Challenge on a randomized track, direction chosen by the car, with no intervention. |
| **Related work** | Iteration log v1.3, v2.4, v3.2; [ERR-02](#err-02--wall-error-goes-blind-at-high-yaw), [ERR-05](#err-05--ultrasonic-beam-cone-bounces-off-the-corner) |
| **Acceptance criteria** | 3 laps / 12 corners completed · track direction latched automatically (no pre-set) · no wall contact · finishes inside the start section · the full 30-point clean score · within the 3-minute round limit · zero human intervention. |
| **Current record** | 10 complete runs from varied start positions and field configurations after the corner-detection work; ~12 s per run at 60 % motor. |
| **Evidence pending** | Per-run video links · exact commit SHA per run · CW/CCW split across the 10 runs · battery voltage before/after. |
| **Status** | **Partially validated** — the bar is met; the run-by-run evidence is not yet logged. |

#### MIL-02 — Obstacle avoidance, standard layouts

| | |
|---|---|
| **Objective** | Complete the Obstacle Challenge on layouts where no pillar straddles the corner sightline: every pillar passed on the WRO-correct side. |
| **Related work** | Iteration log v2.3, v2.5, v2.8, v2.9, v3.0; [ERR-06](#err-06--the-car-pivoted-in-place-instead-of-arcing), [ERR-07](#err-07--recuperando-trigger-tied-to-assumed-linear-speed) |
| **Acceptance criteria** | 3 laps / 12 corners · every pillar passed on the correct side (red → pass on its right, green → on its left) · no pillar contact · no wall contact · segmented turns (`CRUCERO → MANIOBRA`) complete without an outer-wall hit · within the 3-minute round limit · zero intervention. |
| **Current record** | Passes reliably on standard layouts. The pivot-trap fix was confirmed clean at session orillas 417 — both pillars cleared, all 12 turns. Parking not included (MIL-04). |
| **Evidence pending** | Clean-run / attempt count · video · the specific layouts run · RECUPERANDO true-fire / false-fire tally from the HUD footage. |
| **Status** | **Under test** — very close; the outstanding gap is full layout coverage (MIL-03). |

#### MIL-03 — Obstacle Challenge, full layout coverage

| | |
|---|---|
| **Objective** | The MIL-02 result across *every* WRO-legal pillar layout — including a pillar right at the corner mouth or straddling the corner sightline. |
| **Related work** | [ERR-09](#err-09--separating-my-straight-from-the-next-straight-open); iteration log v3.1 (mid-turn detector, logging only) |
| **Acceptance criteria** | As MIL-02, held across the full layout space, with no regression on standard layouts. |
| **Current record** | Not met. Blocked on the *mine vs. beyond* classification ([ERR-09](#err-09--separating-my-straight-from-the-next-straight-open)) — a pillar visible over the corner is sometimes assigned to the wrong straight. The mid-turn detector runs in log-only mode to measure its reliability before it is wired in. |
| **Status** | **In progress** — current focus. |

#### MIL-04 — Parking maneuver

| | |
|---|---|
| **Objective** | After the final lap of the Obstacle Challenge, park fully inside the marked bay. |
| **Related work** | §4.8 (Parking maneuver — in development) |
| **Acceptance criteria** | Vehicle fully within the parking-bay limits · no contact with the bay walls · within the 3-minute round time limit. |
| **Current record** | Not started — the parking algorithm is not yet designed. Full obstacle-round completion (MIL-03) comes first. |
| **Status** | **Not started.** |

---

# 7. How to Build & Run

### 7.1 Hardware requirements

- Raspberry Pi 4 (2 GB+), Raspberry Pi Camera + NoIR wide-angle lens (~120°)
- ESP32 DevKit
- HC-SR04 × 3 (left, right, front) + 5 V↔3.3 V level shifter
- MPU-6050 IMU
- SG90 servo, N20 50:1 DC motor, TB6612FNG driver
- 3S LiPo 2200 mAh, MINI560 step-down
- Start button (Pi GPIO 17), status LED (Pi GPIO 27)

Wiring and board: [`schemes/schematic.png`](schemes/schematic.png), [`schemes/pcb_render.png`](schemes/pcb_render.png), [`electrical/PCB_dimensions.png`](electrical/PCB_dimensions.png), walked through in [§3.3](#33-pcb--wiring); the full KiCad project is under [`electrical/WRO_RevA/`](electrical/WRO_RevA/).

**Pin map (ESP32):** HC-SR04 L `TRIG 27 / ECHO 32`, R `TRIG 26 / ECHO 35`, F `TRIG 14 / ECHO 33`; motor `PWMA 23 / A1 18 / A2 19`; servo `13`; MPU-6050 on I²C; UART to Pi on `Serial2 RX 17 / TX 16`.

### 7.2 ESP32 firmware

```bash
arduino-cli core install esp32:esp32
arduino-cli lib install "MPU6050_tockn"

# Obstacle Challenge (segmented turns) is the default. For the Open Challenge,
# set  const bool rondaObstaculos = false;  near the top of the sketch.

arduino-cli compile --fqbn esp32:esp32:esp32 src/ESP32/PurePursuit/PurePursuit.ino
arduino-cli upload  -p COM5 --fqbn esp32:esp32:esp32 src/ESP32/PurePursuit/PurePursuit.ino
```

Replace `COM5` with your port. `src/ESP32/Controller_PI/Controller_PI.ino` is the older Open-only firmware, kept for reference.

### 7.3 Raspberry Pi software

```bash
git clone https://github.com/Nakashima26/WRO_FE_2026_FoxRobotics.git FoxRobotics
cd FoxRobotics
python3 -m venv .venv && source .venv/bin/activate
pip install -r requirements.txt
# System packages (apt, not pip): python3-smbus, libcamera + gstreamer1.0-libcamera
#   (the camera pipeline in vision.open_camera)
# Enable the camera: sudo raspi-config → Interface Options → Camera
```

[`requirements.txt`](requirements.txt) lists the Python runtime dependencies with minimum versions and documents the apt / Arduino packages that live outside pip. To pin the exact set from the competition Pi, run `pip freeze > requirements.lock.txt` there.

### 7.4 Calibration (before each venue)

All commands run from `src/RASPI/cam/`. Full guide: [`pure_pursuit/INSTRUCCIONES.md`](src/RASPI/cam/pure_pursuit/INSTRUCCIONES.md).

```bash
# 1. BEV homography — place 9 floor markers on the 3×3 grid in config.py, then:
python -m pure_pursuit.calibrate          # C to freeze, click P1..P9, S to save → bev_calib.npz

# 2. HSV ranges for the venue lighting — edit pure_pursuit/config.py (floor / orange line)
#    and vision.py (red / green pillars)

# 3. Vision-only sanity check (no ESP32, no motors)
python -m pure_pursuit.test_vision                 # live camera
python -m pure_pursuit.test_vision --video clip.mp4 # recorded clip
```

### 7.5 Run

```bash
cd src/RASPI/cam
python -m pure_pursuit.runtime_nuevo                       # with debug window
python -m pure_pursuit.runtime_nuevo --no-window           # competition (headless)
python -m pure_pursuit.runtime_nuevo --serial-port /dev/serial0 --record-orillas
```

Startup: the LED on GPIO 27 lights → press the button on GPIO 17 → camera warm-up → `READY` handshake with the ESP32 → the car starts. It stops itself after 12 counted turns (3 laps).

### 7.6 Autostart & deployment

```bash
sudo ./scripts/install_autostart_pi.sh
```

installs `deploy/systemd/wro-runtime.service`, which runs `pure_pursuit/runtime_nuevo.py` on boot (headless, with HUD recording to `videos_orillas/`). Logs: `journalctl -u wro-runtime.service -f`.

`.github/workflows/deploy-pi.yml` is a CI job that, on every push to `main`, SSHes into the Pi, runs `git pull`, and restarts the runtime and VNC services.

---

# 8. Repository Structure

```
FoxRobotics/
├── src/
│   ├── RASPI/
│   │   ├── cam/
│   │   │   ├── vision.py                  # OpenCV HSV pillar detection (red / green) + shape filter
│   │   │   ├── wro_runtime.py             # Legacy Open runtime + shared infra
│   │   │   │                              #   (threaded capture, SerialLink, async video writer)
│   │   │   ├── wro.py                     # Legacy challenge / obstacle logic (superseded)
│   │   │   ├── controlPI.py Serial.py DistGyro.py calibration.py   # legacy helpers
│   │   │   ├── pure_pursuit/              #  ← CURRENT competition software
│   │   │   │   ├── runtime_nuevo.py       # Entry point: Pure Pursuit + rolling obstacle memory
│   │   │   │   ├── runtime.py             # Pure Pursuit without the rolling memory
│   │   │   │   ├── config.py              # All tunables — HSV, look-ahead, gains, triggers
│   │   │   │   ├── bev.py / calibrate.py / bev_calib.npz   # Bird's-eye-view homography (9-pt)
│   │   │   │   ├── centerline.py          # BEV floor mask → drivable centerline (asymmetric keep-out)
│   │   │   │   ├── controller.py          # Geometric Pure Pursuit controller (adaptive look-ahead)
│   │   │   │   ├── obstacle_memory.py     # Sparse rolling obstacle map, IMU-rotated dead reckoning
│   │   │   │   ├── corner_lines.py        # Orange corner-line + turn-direction + mine/beyond
│   │   │   │   ├── mid_turn.py            # Cone-during-turn detector (Phase 1: logging only)
│   │   │   │   ├── far_hint.py            # Early steering hint for far pillars
│   │   │   │   ├── planner.py             # Rollout planner (experimental, not in the main loop)
│   │   │   │   ├── test_vision.py / pure_pursuit_sim.py   # bench + offline sim
│   │   │   │   └── INSTRUCCIONES.md       # Calibration + run guide
│   │   │   ├── pista/                     # Track-edge detection / recording
│   │   │   └── _archive/                  # Superseded runtimes
│   │   └── tests/                         # UART diagnostics + kinematic simulation
│   └── ESP32/
│       ├── PurePursuit/PurePursuit.ino    #  ← CURRENT firmware — V2 protocol, 6-state FSM
│       ├── Controller_PI/Controller_PI.ino# Legacy Open-only firmware (cascade PID + 3-state FSM)
│       ├── _archive/                      # Previous firmware iteration
│       └── TestCodes/                     # Per-peripheral bring-up sketches (servo, gyro, motor, US, serial)
│
├── electrical/WRO_RevA/                   # KiCad project — schematic, PCB layout, 3D models
├── schemes/                               # schematic.png, pcb_render.png (see README §3.3)
├── models/
│   ├── CAD/                               # SolidWorks parts + assemblies
│   ├── STL/                               # 3D-printable parts
│   └── renders/                           # Isometric PNG renders (README §2.5)
├── deploy/
│   ├── systemd/wro-runtime.service        # Pi autostart → runs pure_pursuit/runtime_nuevo.py
│   └── systemd/wro-vnc.service            # VNC for the live camera view
├── scripts/install_autostart_pi.sh        # Installs the systemd service on the Pi
├── .github/workflows/deploy-pi.yml        # CI: push to main → git pull + service restart on the Pi
├── remote/                                # client/server remote-control helper (bench use)
├── videos_orillas/                        # Recorded HUD run footage (debug)
├── t-photos/                              # Team photos            (pending upload)
├── v-photos/                              # Vehicle photos         (pending upload)
├── video/video.md                        # Competition run video links
├── requirements.txt                      # Pi Python dependencies (+ apt / Arduino notes)
├── README.md
└── ENGINEERING_JOURNAL.md                # Dated, phase-by-phase build log (companion to §5.3 / §6.5)
```

---

# 9. Videos

| Challenge | Link |
|---|---|
| Open Challenge — 3 laps autonomous | [YouTube](https://youtu.be/orP-BNSG-6s) |

> Full video index: [`video/video.md`](video/video.md)

---

# 10. Photos

Full-size images are in [`v-photos/`](v-photos/) (vehicle) and [`t-photos/`](t-photos/) (team).

<table>
  <tr>
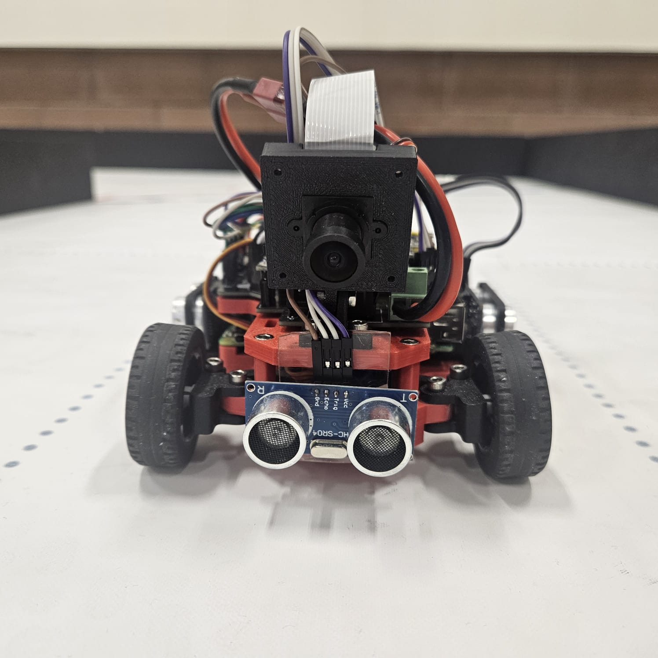
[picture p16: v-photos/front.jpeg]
Front view
    <td align="center"><br><b>Front</b></td>
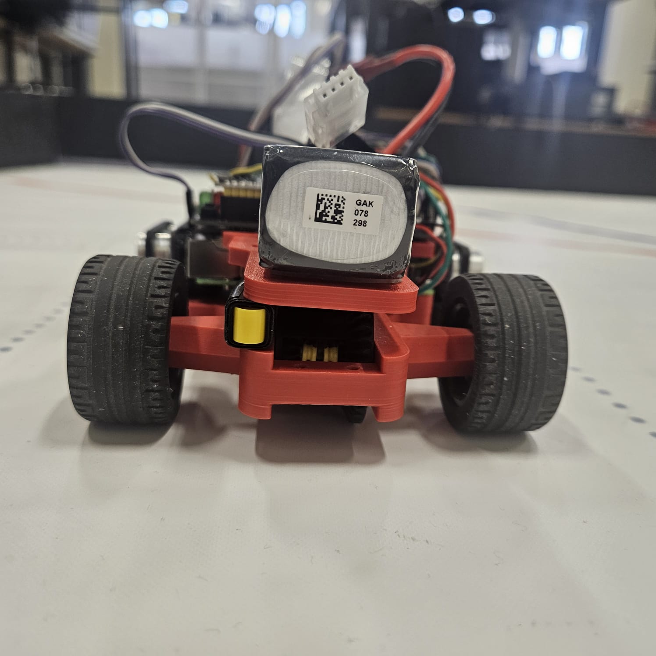
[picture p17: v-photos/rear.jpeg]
Rear view
    <td align="center"><br><b>Rear</b></td>
  </tr>
  <tr>
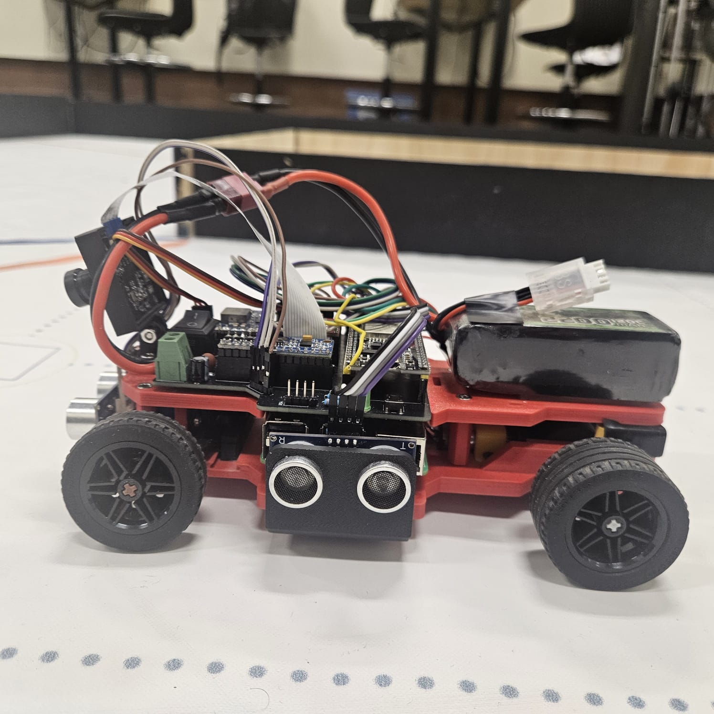
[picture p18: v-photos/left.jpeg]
Left side
    <td align="center"><br><b>Left side</b></td>
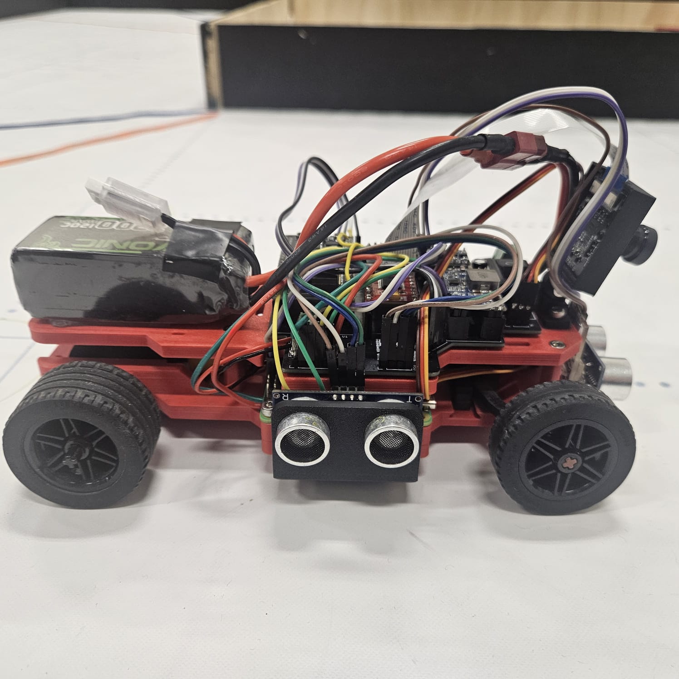
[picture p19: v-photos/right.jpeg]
Right side
    <td align="center"><br><b>Right side</b></td>
  </tr>
  <tr>
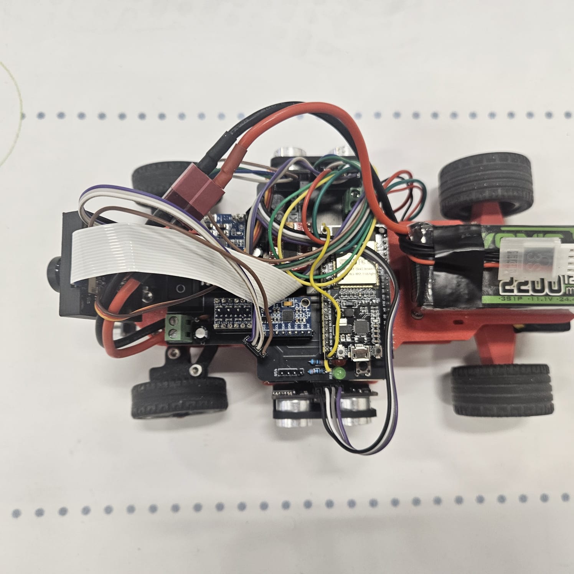
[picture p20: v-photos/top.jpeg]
Top view
    <td align="center"><br><b>Top</b></td>
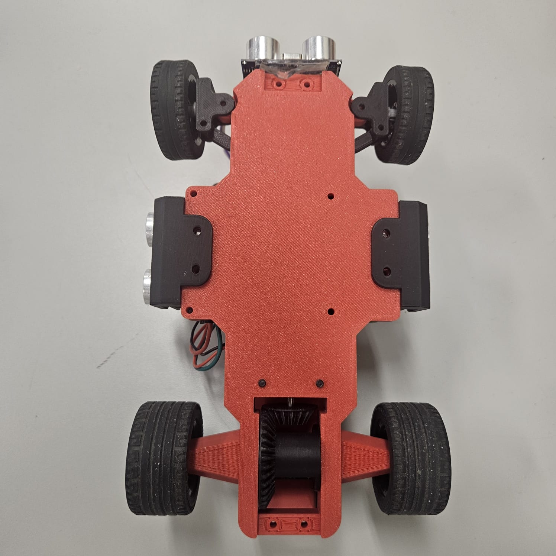
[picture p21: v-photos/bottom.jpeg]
Bottom / undercarriage
    <td align="center"><br><b>Bottom (undercarriage)</b></td>
  </tr>
  <tr>
    <td align="center">Isometric view<br><b>Isometric</b></td>
    <td align="center"><i>Team photo — <code>t-photos/team.jpeg</code> (pending)</i></td>
  </tr>
</table>

---

## License

Released under the [MIT License](LICENSE) — free to use, modify and build on, code and documentation alike, with attribution.

This repository is public as required by WRO Future Engineers rules and will remain public for at least 12 months after the competition.

*WRO Future Engineers 2026 — FoxRobotics — México*

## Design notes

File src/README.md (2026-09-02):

Control software
====

This directory contains the competition software used by the vehicle. See the
[top-level README](../README.md) (§4) for the full architecture.

Two controllers:

- **Raspberry Pi** — vision + Pure Pursuit path planning.
  Current code: [`RASPI/cam/pure_pursuit/`](RASPI/cam/pure_pursuit/),
  entry point [`runtime_nuevo.py`](RASPI/cam/pure_pursuit/runtime_nuevo.py).
  Legacy Open-only runtime: [`RASPI/cam/wro_runtime.py`](RASPI/cam/wro_runtime.py).
- **ESP32** — real-time FSM, cascade PID, actuators.
  Current firmware: [`ESP32/PurePursuit/PurePursuit.ino`](ESP32/PurePursuit/PurePursuit.ino).
  Legacy firmware: [`ESP32/Controller_PI/Controller_PI.ino`](ESP32/Controller_PI/Controller_PI.ino).

## Run commands

### Raspberry Pi

Start the runtime (from `src/RASPI/cam/`):

```bash
cd ~/FoxRobotics
source .venv/bin/activate
cd src/RASPI/cam
python -m pure_pursuit.runtime_nuevo
```

Headless (competition) with track-edge recording:

```bash
python -m pure_pursuit.runtime_nuevo --no-window --serial-port /dev/serial0 \
    --record-orillas --record-output ~/FoxRobotics/videos_orillas
```

Calibration and vision-only testing: see
[`RASPI/cam/pure_pursuit/INSTRUCCIONES.md`](RASPI/cam/pure_pursuit/INSTRUCCIONES.md).

### ESP32

Flash once, then it runs on boot. For the Open Challenge set
`const bool rondaObstaculos = false;` near the top of the sketch first.

```powershell
arduino-cli core update-index
arduino-cli core install esp32:esp32
arduino-cli lib install "MPU6050_tockn"
arduino-cli compile --fqbn esp32:esp32:esp32 src/ESP32/PurePursuit/PurePursuit.ino
arduino-cli upload -p COM5 --fqbn esp32:esp32:esp32 src/ESP32/PurePursuit/PurePursuit.ino
```

Replace `COM5` with your ESP32 port.

### Autostart on Raspberry Pi

```bash
chmod +x /home/user/FoxRobotics/scripts/install_autostart_pi.sh
/home/user/FoxRobotics/scripts/install_autostart_pi.sh
```

Installs `deploy/systemd/wro-runtime.service`, which runs
`pure_pursuit/runtime_nuevo.py` on boot.

All artifacts required to resolve dependencies and build the project must be
included in this directory as well.

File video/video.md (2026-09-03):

# FoxRobotics — WRO 2026 Future Engineers

## Open Challenge — 3 laps autonomous

Open Challenge (https://youtu.be/orP-BNSG-6s)

[https://youtu.be/orP-BNSG-6s](https://youtu.be/orP-BNSG-6s)

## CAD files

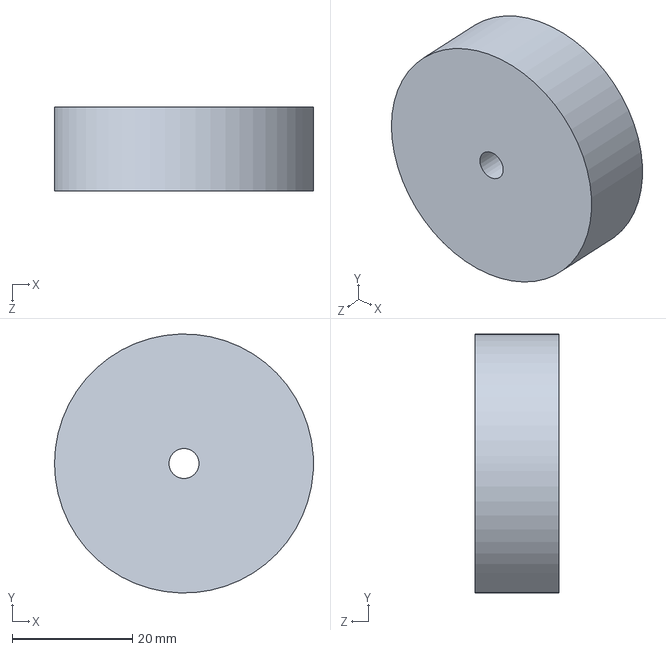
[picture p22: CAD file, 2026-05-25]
models/CAD/RuedaEnfrente.SLDPRT
43.0 x 43.0 x 14.0 mm

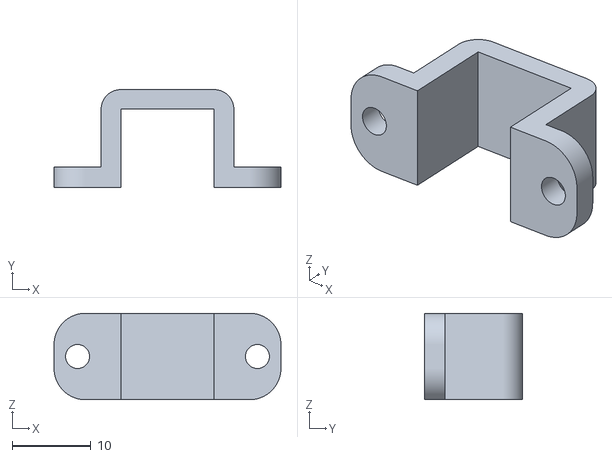
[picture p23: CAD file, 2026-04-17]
models/STL/SoporteDCmotor.STL
28.9 x 12.4 x 11.0

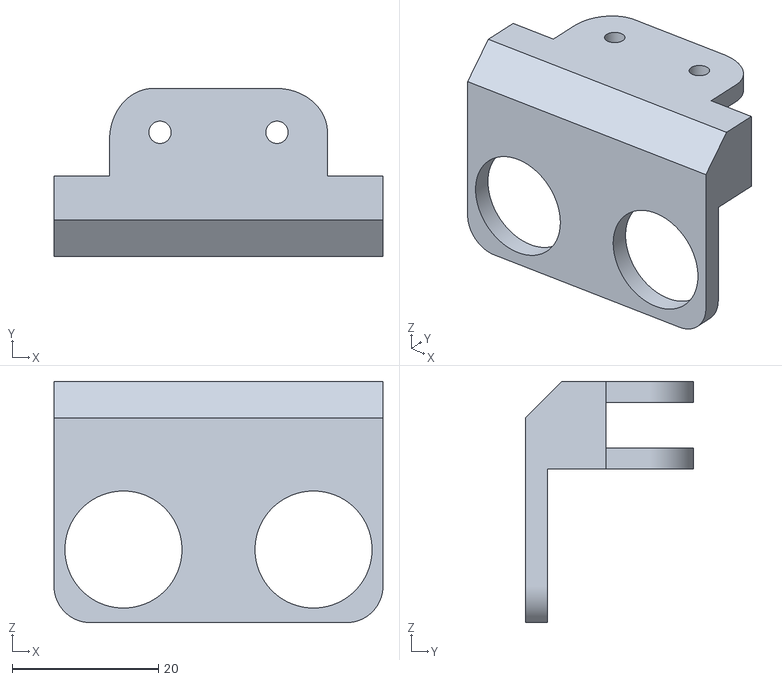
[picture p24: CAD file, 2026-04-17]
models/STL/SoporteUltrasonicoLado.STL
45.0 x 23.0 x 33.0

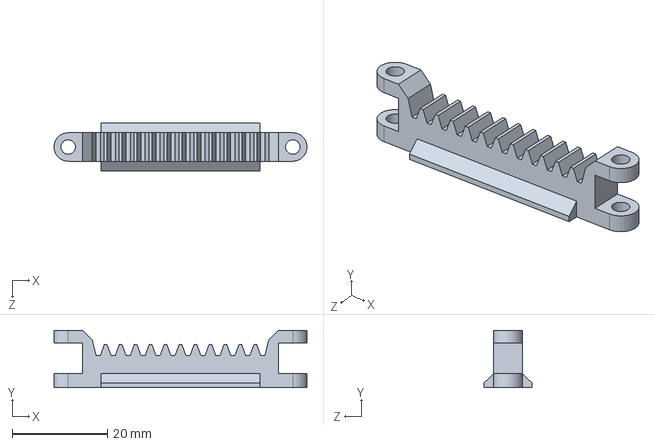
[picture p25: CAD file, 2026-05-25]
models/CAD/Cremallera.SLDPRT
53.1 x 12.0 x 10.0 mm

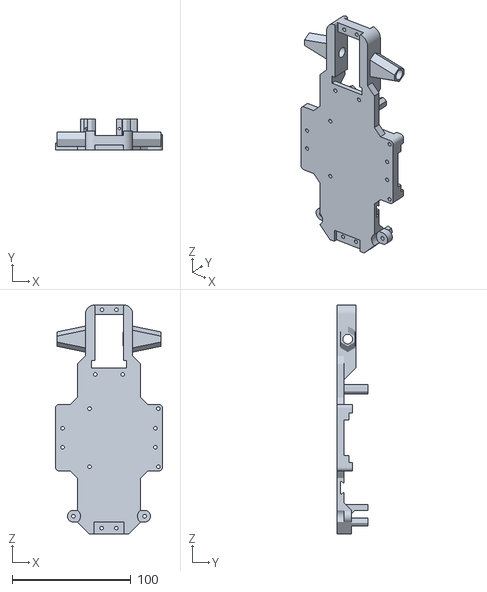
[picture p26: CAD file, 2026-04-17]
models/STL/BaseDireccion.STL
90.2 x 26.0 x 193.0

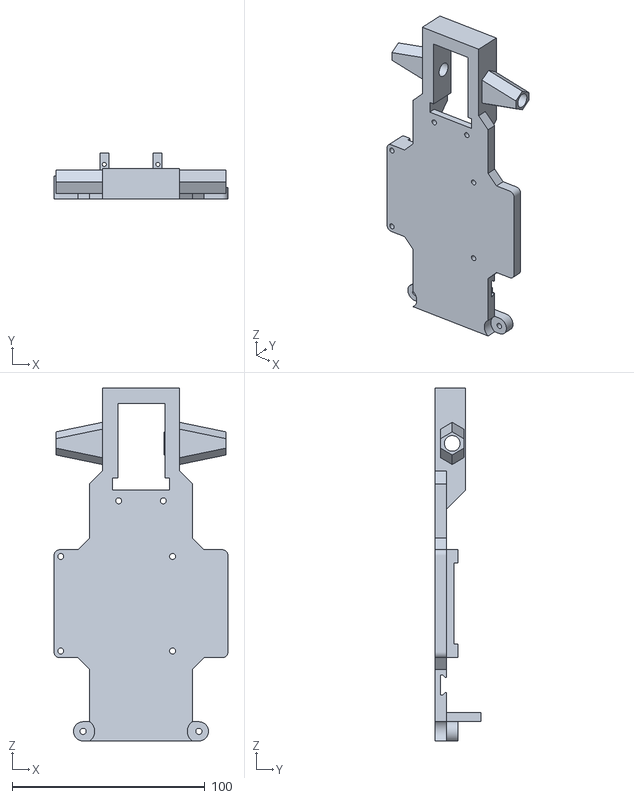
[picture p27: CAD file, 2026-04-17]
models/STL/Chasis.STL
90.2 x 24.0 x 183.0

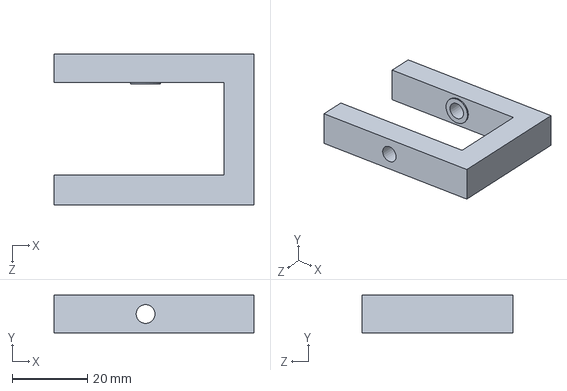
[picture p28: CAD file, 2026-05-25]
models/CAD/SoporteDiff.SLDPRT
53.0 x 10.0 x 40.0 mm

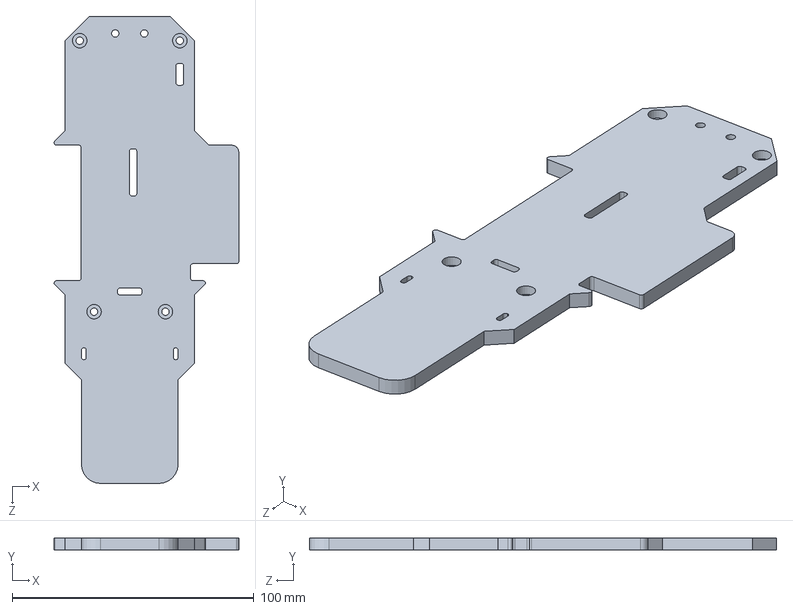
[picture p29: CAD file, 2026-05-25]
models/CAD/TopShell.SLDPRT
76.4 x 5.00 x 193.0 mm

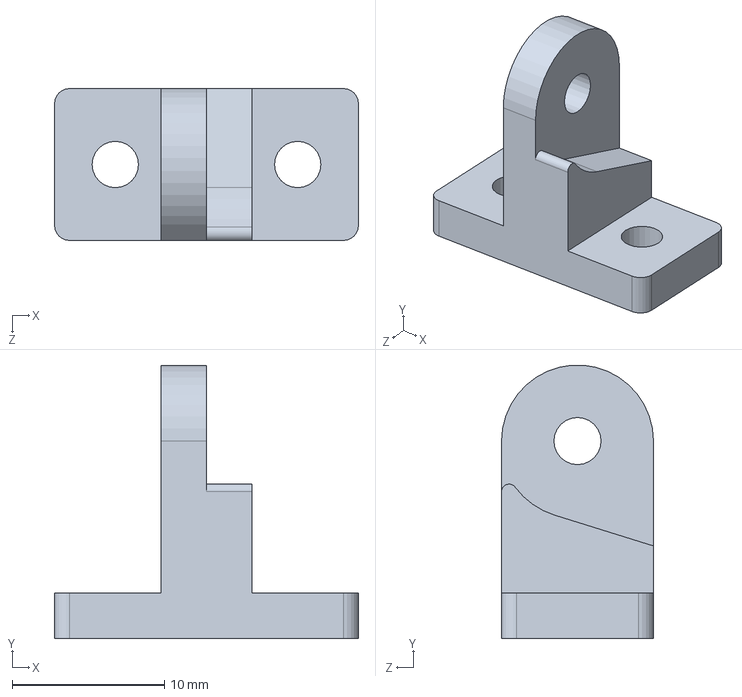
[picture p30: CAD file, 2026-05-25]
models/CAD/CameraBase.SLDPRT
20.0 x 18.0 x 10.0 mm

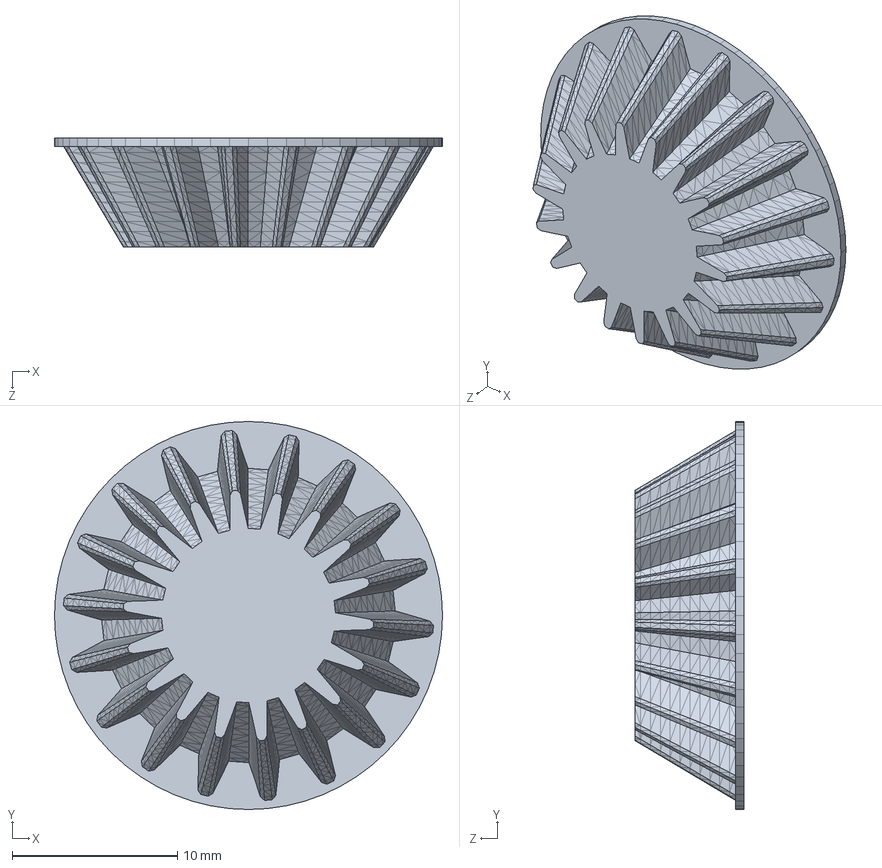
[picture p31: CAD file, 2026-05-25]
models/CAD/pinion.SLDPRT
23.5 x 23.5 x 6.59 mm

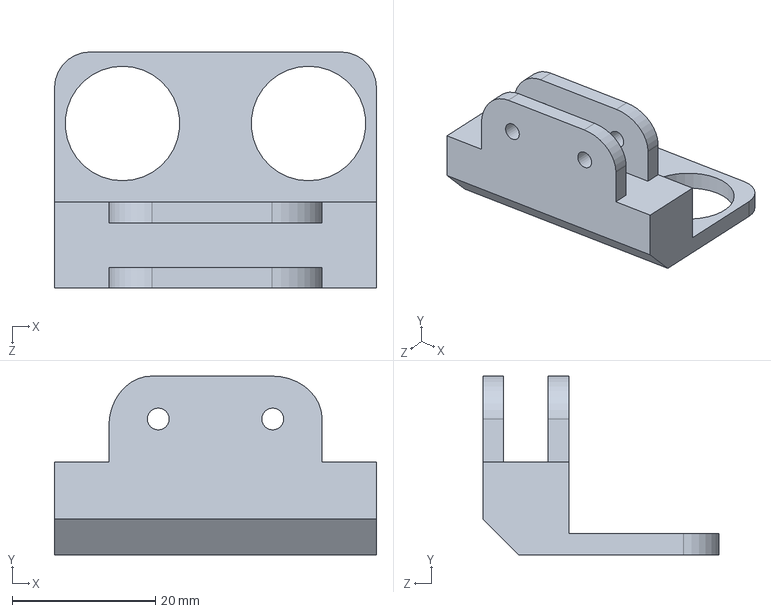
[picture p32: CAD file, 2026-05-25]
models/CAD/UltrasonicSupport.SLDPRT
45.0 x 25.0 x 33.0 mm

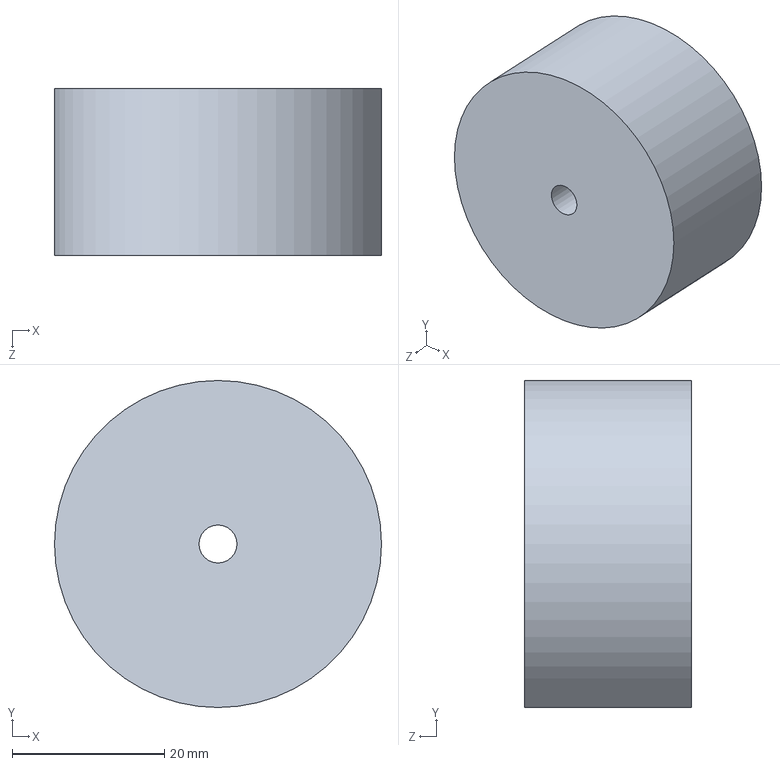
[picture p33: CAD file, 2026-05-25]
models/CAD/RuedaAtras.SLDPRT
43.0 x 43.0 x 22.0 mm

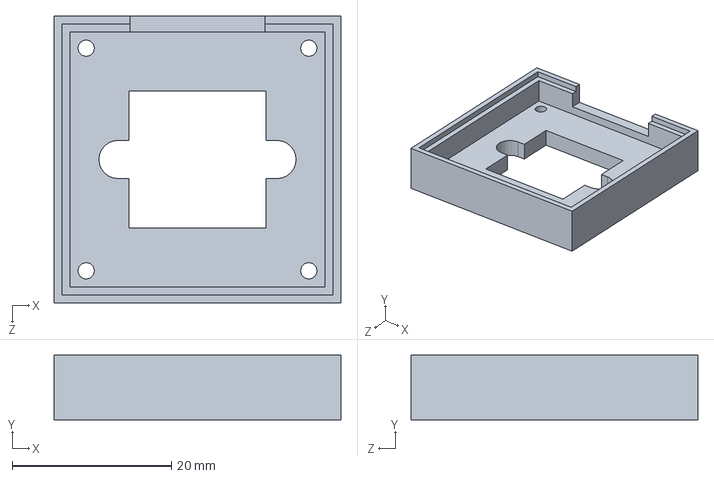
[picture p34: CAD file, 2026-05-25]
models/CAD/CameraFrnt.SLDPRT
36.1 x 8.15 x 36.1 mm

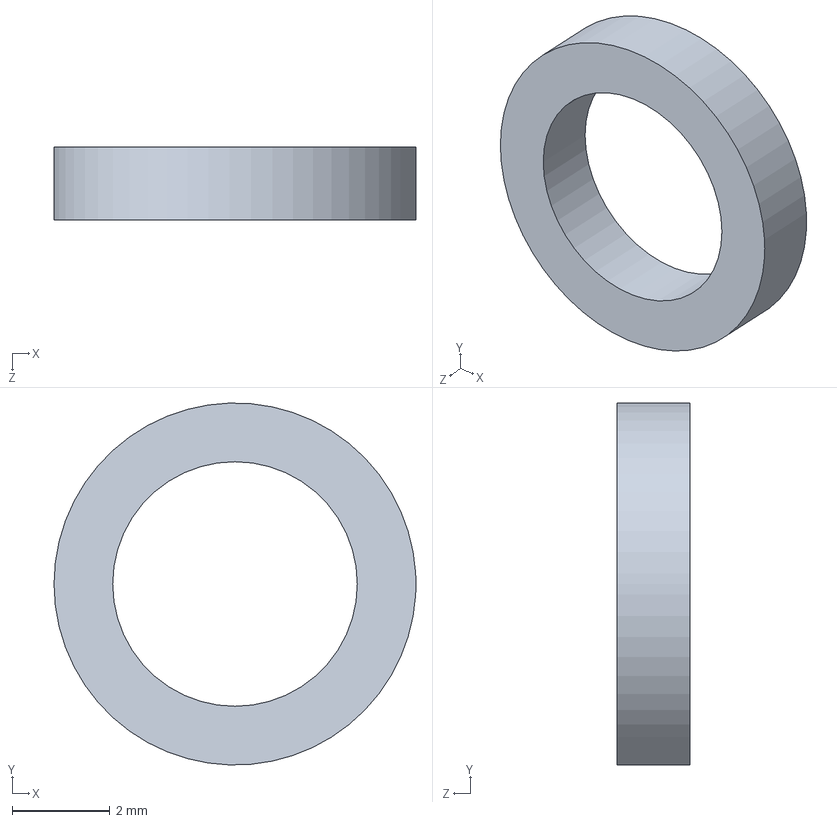
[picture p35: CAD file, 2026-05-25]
models/CAD/TuercaLego.SLDPRT
7.40 x 7.40 x 1.50 mm

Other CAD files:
models/CAD/ServoGearDirection.SLDASM
models/CAD/Direccional.SLDASM
models/CAD/BaseChasis.SLDPRT
models/CAD/DCsupport.SLDPRT
models/CAD/CameraBack.SLDPRT
models/CAD/HC-SR04 Ultrasonic sensor.SLDPRT
models/CAD/LinkageDireccion.SLDPRT
models/CAD/ServoGearDirection.SLDPRT
models/CAD/SteeringKnuckle.SLDPRT
models/CAD/pila.SLDPRT
models/STL/Cremallera.STL
models/STL/ServoGearDirection.STL
models/STL/TopShell.STL
models/STL/pinion.STL

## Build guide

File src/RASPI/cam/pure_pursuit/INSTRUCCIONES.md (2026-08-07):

 # Pure Pursuit — Instrucciones de uso

Todos los comandos se corren desde `src/RASPI/cam/`.

---

## 1. Calibrar la cámara (una sola vez)

Necesitas la cámara montada en su posición final en el robot, apuntando al piso.

Coloca 4 marcadores físicos (papel, cinta) en el suelo en estas posiciones relativas al eje delantero del robot:

| Punto | Lateral | Adelante |
|---|---|---|
| A | 10 cm izquierda | 20 cm |
| B | 10 cm derecha | 20 cm |
| C | 15 cm izquierda | 38 cm |
| D | 15 cm derecha | 38 cm |

```bash
python -m pure_pursuit.calibrate
```

1. Se abre una ventana con la cámara en vivo
2. Presiona `C` para congelar el frame
3. Haz clic en los 4 marcadores en orden: A → B → C → D
4. Se abre una segunda ventana con la vista BEV en tiempo real — verifica que se vea bien
5. Presiona `S` para guardar → genera `pure_pursuit/bev_calib.npz`
6. Presiona `R` para rehacer si los puntos quedaron mal

> Si mueves o cambias el ángulo de la cámara, repite este paso.

---

## 2. Calibrar colores HSV (antes de cada competencia)

La iluminación del venue cambia los colores. Ajusta los rangos en `config.py`:

```python
# Piso blanco WRO
FLOOR_LOWER = np.array([0,   0,  160])
FLOOR_UPPER = np.array([180, 50, 255])
```

Si el blanco del piso se ve grisáceo o amarillento bajo las luces del venue, baja `FLOOR_LOWER[2]` hasta 140 o 120.

Los rangos de rojo y verde están en `vision.py` (el archivo de visión principal).

---

## 3. Probar solo la visión (sin robot, sin ESP32)

Útil para verificar que la BEV y la centerline se ven bien antes de conectar todo.

```bash
python -m pure_pursuit.test_vision
```

Con un video grabado en lugar de cámara en vivo:
```bash
python -m pure_pursuit.test_vision --video ruta/al/video.mp4
```

Lo que deberías ver:
- Ventana izquierda: cámara con los obstáculos detectados (rojo/verde marcados)
- Ventana derecha: BEV con la centerline en cyan, punto look-ahead en amarillo, robot en naranja
- Texto arriba: `pp=ON`, ángulo de dirección, cantidad de puntos del path

Presiona `S` en cualquier momento para guardar un screenshot.
Presiona `ESC` para salir.

---

## 4. Correr en el robot real

### Requisitos previos
- `bev_calib.npz` generado (paso 1)
- ESP32 con `PurePursuit.ino` ya flasheado
- Pi conectada al ESP32 por Serial2 (RX=17, TX=16)

### Comando

```bash
python -m pure_pursuit.runtime
```

### Secuencia de arranque automática
1. LED en GPIO27 enciende → Pi lista
2. Espera que presiones el botón en GPIO17
3. Calienta la cámara ~2 segundos
4. Manda `READY` al ESP32 → ESP32 responde y arranca motores
5. Loop: cámara → BEV → centerline → Pure Pursuit → serial al ESP32

### Flags útiles

```bash
# Sin ventana (en competencia sin monitor)
python -m pure_pursuit.runtime --no-window

# Grabar video de lo que ve la cámara
python -m pure_pursuit.runtime --no-window --record-orillas

# Puerto serial diferente (si usas adaptador USB)
python -m pure_pursuit.runtime --serial-port /dev/ttyUSB0
```

---

## Resumen de archivos

| Archivo | Para qué |
|---|---|
| `calibrate.py` | Calibrar la homografía BEV con la cámara real |
| `test_vision.py` | Probar visión + centerline sin robot ni serial |
| `runtime.py` | Runtime completo para competencia |
| `config.py` | Todos los parámetros ajustables (HSV, lookahead, gains) |
| `bev_calib.npz` | Archivo de calibración generado por calibrate.py |

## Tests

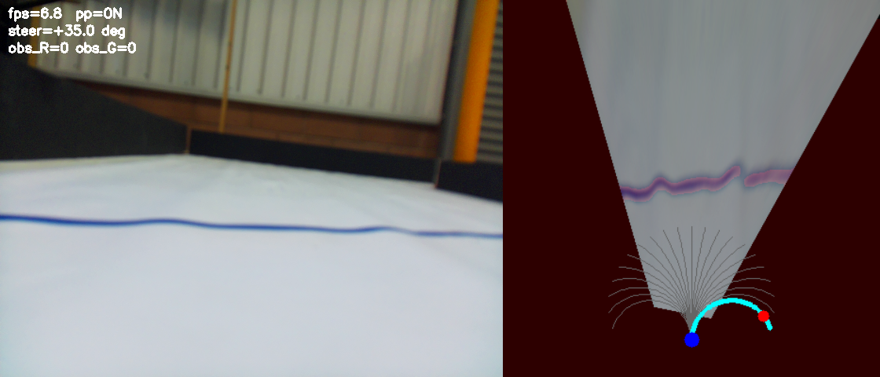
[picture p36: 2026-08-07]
src/RASPI/cam/TEST Vision - camara_BEV_screenshot_22.06000.2026.png

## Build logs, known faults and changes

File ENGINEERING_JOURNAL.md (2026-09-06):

# FoxRobotics — Engineering Journal

> **Team:** FoxRobotics · **Event:** WRO 2026 Future Engineers — Self-Driving Car
> **Region:** México — Baja California

## Team & roles

| Member | Responsibility |
|---|---|
| **Erick Blanco** | Mechanical design; vehicle programming and control — both the Open and the Obstacle rounds |
| **Jesse Banda** | Vehicle programming, primarily computer vision; built the code structure the rest was developed on |
| **César Emiliano Ahumada** | Electrical bring-up and testing; schematic and PCB design |
| **Daniel Millán** | Coach |

Dated, chronological record of the build. It is the **timeline** companion to the two
thematic views in the [README](README.md):

- [§5.3 Iteration log](README.md#53-iteration-log) — structural changes by topic, with status.
- [§6.5 Milestones](README.md#65-milestones) — M1–M11 with acceptance criteria.
- [§5.5 Failure & Incident log](README.md#55-failure--incident-log) — post-mortems `ERR-01…ERR-09`.

Where an entry maps to one of those, it is cross-referenced rather than repeated.

**Sources & conventions**

- The **pre-repo period** (late March – early May 2026) is reconstructed from the team's
  design notes and is marked *(reconstructed)*.
- From 2026-04-13 onward, entries are anchored to **git history on `main`** (short hashes
  link into the log) and to the numbered on-track test sessions (`orillasNNN`) — the
  session counter has incremented on every integrated run since June 2026 and is now
  around **700**, so most tuning happened between commits, not in them.
- **branch** marks work implemented on a feature branch (`Workin`, `SectionTurning`,
  `ParedCenterline`) and not yet merged to `main`.

---

## Phase 0 — Vehicle design & per-peripheral bring-up *(reconstructed; pre-repo)*

**Focus:** one reliable vehicle, architecture fixed before any code — Raspberry Pi 4 for
vision, ESP32 for all real-time I/O ([README §1.1](README.md#11-design-goals)).

### 2026-03-30 → 04-05 — Semana Santa design week
A full week on the vehicle before anything else: SolidWorks CAD of the whole car, fit
checks and tolerance checks on every mating part, packaging the chassis around the
electronics (Raspberry Pi 4 first). Decisions locked here and never revisited: two-controller
split (Pi 4 + ESP32), rack-and-pinion Ackermann steering, rear-wheel drive with a printed
open differential, ~20 × 10 cm footprint for obstacle-field clearance.
→ [README §2](README.md#2-mechanical-design--mobility), [§2.4](README.md#24-steering--rack-and-pinion-with-ackermann-geometry).

### 2026-04 — Chassis, base wiring, PCB layout started
Chassis printed in PLA on a Bambu Lab A1 and assembled with LEGO axles/wheels
(**M1**). Base circuit designed and validated on a breadboard (**M3**). Custom PCB
laid out to fit the finished mechanical model — designed *after* the CAD, not before
(**M4**). → [README §3.3](README.md#33-pcb--wiring).

### 2026-04-13 → 04-27 — First commits: CAD + PCB
Repository created (git started well after the project did). CAD model, schematic, and
PCB shape committed; routing begun.
`283078e` · `ade099b` · `c9ce1e2` · `7e2a3d3` · `51ea239` (final PCB shape) · `f015e0d` (routing).

### ~2026-04-25 → 05-09 — Per-peripheral ESP32 bring-up
Each sensor and actuator bench-tested in isolation with a dedicated sketch, ESP32 only —
each HC-SR04, the servo, the DC motor, gyro read, serial echo
([`src/ESP32/TestCodes/`](src/ESP32/TestCodes/)) (**M2**). First combined controller
sketch alongside them. By 2026-05-09 this produced a **slightly functional Open-round
car running on the ESP32 alone** (no Raspberry Pi yet). `6474f65` (TestCodes +
FirstController).

---

## Phase 1 — First closed-loop Open Challenge run (May 2026)

**Focus:** get the car around the track on wall following alone.

### 2026-05-09 — First working Open-round controller
Single-loop PID on `distL − distR`, two VL53L0X ToF sensors, 3-state FSM
(`Controller_PI.ino`). First lap capability. `61544cb`.
→ [README iteration log "First firmware"](README.md#53-iteration-log).

### 2026-05 — `ERR-01`: ToF lost the black wall
Against the matte-black outer wall the VL53L0X range collapsed past ~70 cm; white walls
read fine. Reproduced on the bench with a single sensor, so not a wiring fault. **Both
channels switched to HC-SR04 ultrasonic** — traded ±3 mm for ±15 mm and closed the gap in
software later. → [README ERR-01](README.md#err-01--vl53l0x-lost-the-black-wall-past-70-cm).

### 2026-05 — `ERR-02`: wall error goes blind at high yaw
On corner entry the car drifted into a wall while the PID output stayed small: the
HC-SR04 beam cone hits the wall obliquely once yawed, both sides over-report, `distL − distR`
sits near zero. Motivated the **cascade PID** (outer wall→heading, inner heading→servo via
IMU) built over the next weeks. → [README ERR-02](README.md#err-02--wall-error-goes-blind-at-high-yaw),
[§4.6](README.md#46-cascade-pid-always-running-underneath).

### 2026-05-23 — Camera bring-up
Pi camera wired; track-edge (`detect_orillas.py`) detection and the BEV calibration tool
scaffolded; threaded recorder added so runs are reviewable. Many same-day iterations.
`21fe8df` · `5797487` · `345b430` (`record_orillas.py`).

### 2026-05-25 → 05-26 — Repo reorganized, first README
`src/` and `models/` restructured; first README written.
`6a448ca` · `ea70bfc` · `dde0543` · `a3b2fe6`.

---

## Phase 2 — Two controllers, one link (June 2026)

**Focus:** split vision and real-time control across the two processors and make the link
survive latency.

### 2026-06-04 → 06-05 — Integration pass + UART diagnostics
Vision, `wro_runtime.py`, and `Controller_PI.ino` wired end-to-end. UART framing tools
added (`diagnose_uart.py`, `test_serial_debug.py`, `test_uart_simple.py`); dead code
parked; `wro-runtime.service` drafted. `0a9251f` · `9169693` · `d6f677a` · `a8345dd`.

### 2026-06-08 → 06-09 — Two-controller split formalized + deploy infra
VNC for live view on the Pi; a self-hosted GitHub Actions runner and push-to-deploy CI;
an 800 ms timeout so a late packet makes the ESP32 reuse the last command instead of
stalling. `69f82a9` · `a065d78`.
→ [README §4.1](README.md#41-system-overview--two-controllers-one-link),
[§5.2 trade-off 1](README.md#52-key-engineering-trade-offs).

### 2026-06-11 → 06-13 — Pure Pursuit workspace
`FixedController` for the Open round (`711c6ec`); `pure_pursuit/` scaffold with
`INSTRUCCIONES.md` and `calibrate.py` (`95f3744`).

### 2026-06-22 — Centerline extraction + geometric Pure Pursuit
Floor-colour centerline in the BEV, first `PurePursuit.ino`, first `centerline.py`.
Replaces the reactive pillar-offset PID, which over-reacted near and under-reacted far.
`79706be` (camera-duplicate fix) · `e494d8c` (centre algorithm) · `556266b`.
→ [README iteration log v2.0](README.md#53-iteration-log),
[§4.3](README.md#43-vision-pipeline-raspberry-pi--pure_pursuit).

### 2026-06-25 — Last commit before the July break
`2b0f82d`. Repo quiet until 2026-08-07.

---

## Phase 3 — Wide lens & white balance (July – 2026-08-07)

### 2026-07 (first week) — Lens swap 63° → 120°
Wide-angle NoIR lens arrived in the first week of July, so the camera sees far enough
ahead to read a pillar and the corner on the same frame. The rest of that period went to
bench tests aimed at removing the reddish cast it introduced (see `ERR-03` below).

### 2026-08-07 — `ERR-03`: red cast on every frame
The NoIR lens has no IR-cut filter; every frame came out heavily red-tinted and all HSV
masks broke. Fixed by pinning libcamera white balance
(`awb-enable=false colour-gains=<1.2,1.5>`) and re-tuning the red/green ranges on the
corrected image. Also a first pass at a false-turn bug.
`9ada7a0` (FalseTurn bug) · `140051a` · `945c2f1` (RGB range cleanup).
→ [README ERR-03](README.md#err-03--wide-angle-noir-lens-put-a-red-cast-on-every-frame).

---

## Phase 4 — Sim, calibration, corner lines (2026-08-11 → 08-19)

### 2026-08-11 — Offline kinematic sim
`pure_pursuit_sim.py` (bicycle model of centerline + Pure Pursuit + obstacle memory) and
`runtime_nuevo.py`, so controller logic can be tuned without track time. `0a2c5d2`.
→ [README iteration log v2.1](README.md#53-iteration-log).

### 2026-08-12 — Obstacle detection hardening
`vision.py` shape filtering — area, solidity, aspect ratio — so the mat's coloured lines
are not read as pillars. Several same-day passes.

### 2026-08-13 — BEV calibration 4 → 9 points
RANSAC fit over a 3×3 grid of physical floor markers; a 4-point fit is exact and cannot
reject a mis-click or check reprojection error. `daf1e03` (a batch of `test`/`Revert`
commits precede it — the failed attempts). → [README iteration log v2.2](README.md#53-iteration-log).

### 2026-08-15 — "line memory" tried and reverted
`89f9d51` → `270b783` same day. Kept in the log as a rejected approach.

### 2026-08-17 → 08-19 — Orange / blue ground-line tracking
Row-by-row tracking of the mat's corner lines in the BEV — a turn trigger and a
"my straight vs. the next one" boundary for obstacles. `d3a611e` · `8edc1b8`.
**2026-08-18 was a heavy revert day** — a batch of centerline and `.ino` experiments all
backed out (`663d45b` … `42b397a`); the net keeper was `770c9a3` (RemoverLines).
`d592798` (WallDistance) starts feeding ultrasonic wall distance toward steering.
→ [README iteration log v2.3](README.md#53-iteration-log).

---

## Phase 5 — Wall-aware steering; Open Challenge validated (2026-08-20 → 08-28)

### 2026-08-20 → 08-21 — `ParedCenterline` merged
Centerline biased by ultrasonic wall distance (it drifted toward the outer wall on wide
corners without it); V2 protocol fixes; BetterSteering / BetterDodge passes; ghost-object
handling started. `f5066e1` · `24b2ec7`.
→ [README iteration log v2.4](README.md#53-iteration-log).

### 2026-08-24 — Ghost obstacle after a turn
Cans left in memory after a turn kept a phantom keep-out. First fix reverted, v2 shipped.
`a41ac0e` → `3c96abf`. `333b0e1` ("FreshStart: GirandoStep1") begins a rebuild of the
turn logic.

### 2026-08-25 → 08-27 — Line-classification & centerline tuning stretch
Long run of small commits and reverts on orange/blue line classification and centerline
stability; segmented-obstacle and interior-turn prototypes (`510a89a`, `b55e317`);
turning-detection v2. `fb81fe6` ("back2Basics", 08-27) resets the branch after the
centerline experiments diverged.

### 2026-08-27 — Obstacle-pass pulse fixed; earlier dodge
`ff9c83b` — the `pasado` "obstacle physically cleared" pulse was never firing.
`68aab07` — earlier/stronger dodge and earlier RECUPERANDO. `ab574ab` — rolling-memory
`ds_px` brake on hard turns. `57d3218` — lateral rebase: enter RECUPERANDO when the can
crosses the axis, not when it passes behind.
→ [README iteration log v2.5](README.md#53-iteration-log).

### 2026-08-28 — `ERR-08`: Pi undervoltage → frame-rate rescale
~0.3 V drop on undersized power leads browned out the Pi under load. Re-fed in 22 AWG;
loop went **~7 → ~14 fps**. Half the per-frame knobs were then calibrated at the old rate
and firing twice as fast — every one re-scaled. `e4ca4f9` · `1a19cdb`.
→ [README ERR-08](README.md#err-08--raspberry-pi-undervoltage-from-undersized-power-wiring),
[iteration log v2.7](README.md#53-iteration-log).

### 2026-08-28 — Hot start + run recording
Pipeline runs disarmed during the button delay; the ESP32 is gated on the first real V2
line so the car never rolls on the fallback PID; MJPG `.avi` HUD capture from the moment
the button is pressed. `3245c1c` · `2355caf` · `f257371`.
→ [README iteration log v2.6](README.md#53-iteration-log).

### 2026-08-28 — `ERR-07`: RECUPERANDO anchor drifts (experiments)
The geometric dead-reckoning anchor for the recovery trigger drifted 200–400 mm in
1–2 s and fired early or late; `SPEED_SCALE` at 1.0 / 0.35 / 0.60 all wrong somewhere.
`f24c547` · `25d0565` and their reverts. Resolved the next day.
→ [README ERR-07](README.md#err-07--recuperando-trigger-tied-to-assumed-linear-speed).

### 2026-08-28 — **M8: Open Challenge validated**
10 complete autonomous runs from varied start positions and field configurations, track
direction latched by the car, no wall contact, correct finish, ~12 s per run at 60 %
motor. Focus moves to the Obstacle Challenge.
→ [README MIL-01](README.md#mil-01--open-challenge-full-autonomous-run).
**Evidence still to log:** per-run video links, commit SHA per run, CW/CCW split,
battery voltage before/after.

---

## Phase 6 — Obstacle-round root causes (2026-08-29)

### 2026-08-29 — `ERR-07` fixed: measured-state RECUPERANDO trigger
Anchor retired. New trigger reads state that is already measured — centerline avoidance
weight (ARM), the memory's own "is a can still in the way" test (CLEAR), and a heading
snapshot (SKEW ≥ 25°). A gentle dodge that straightens itself never stops for a recovery.
`52549c8`, then `ab637aa` · `ef40152` · `5eee517` · `0306cfd` · `98da50a` tuning.
→ [README iteration log v2.9](README.md#53-iteration-log).

### 2026-08-29 — `ERR-06` fixed: pivot-trap
Near a can the steer term hit ±0.9 (≈ full lock) so the car pivoted in place instead of
arcing; the can's `y` never advanced, so RECUPERANDO never armed. Fixes: `LOOKAHEAD_MIN_PX`
60 → 78; adaptive look-ahead and steer-gain re-keyed on the **longitudinal** gap;
`forget_color_obstacles()` on a confirmed pass so the centerline un-bends. `1daf563`.
**Confirmed clean at session orillas 417** — both cans cleared, all 12 turns.
→ [README ERR-06](README.md#err-06--the-car-pivoted-in-place-instead-of-arcing),
[iteration log v2.8](README.md#53-iteration-log).

### 2026-08-29 — Orange-line direction, fast verdict
Slope evaluated from the first frame; armed-debounce for a green can seen just after a
turn. `a9acdde` · `13b163b`.

---

## Phase 7 — Hardening, segmented turns, documentation (2026-08-31 → 09-06)

### 2026-08-31 — Exterior cone at the corner mouth
A can right at the corner: drive straight past it, *then* turn, so the blind arc can't
sweep into it. `4e5ca40`. → [README iteration log v2.11](README.md#53-iteration-log).

### 2026-08-31 — Turn direction inferred during the run
`TurnDirectionTracker` — direction latched from the orange corner-line slope while
running, not pre-set at check-in. `3a6735e` · `a72a751` · `e641817`
(`LINE_FIT_MAX_SLOPE_DEG` 45 → 72, one turn sense wasn't fitting).
→ [README iteration log v2.10](README.md#53-iteration-log).

### 2026-08-31 — Camera-safe service restart
CI and ops use `stop → sleep 4 → start`; `systemctl restart` doesn't release the CSI
device and the camera wedges. `9aff6c9`.
→ [README iteration log v2.12](README.md#53-iteration-log).

### 2026-08 → 09 — **branch** work (`Workin`, `SectionTurning`) — not on `main`
- **Segmented obstacle turns** `CRUCERO → MANIOBRA`: cruise to a set front-sensor
  distance, then a forward arc or a reverse pivot chosen from the outer-wall distance;
  a mandatory motor-coast phase before every direction reversal after **`ERR-04`** (a
  reversal with no coast destroyed a TB6612 and an N20). → README iteration log v3.0,
  [ERR-04](README.md#err-04--tb6612-and-motor-destroyed-by-a-reversal-with-no-coast-delay).
- **Mid-turn cone detector** (`mid_turn.py`) — Phase 1, logging only (`[MTURN]`).
  → README iteration log v3.1.
- **Open round on pure wall + gyro PID** — Pi steer ignored; per-round `AngGiro` /
  `MOTOR_MAX`; `giroArmado` corridor-arm; front-wall approach slow-down; `TERMINANDO`
  return-to-start finish. → README iteration log v3.2, `ERR-05`.

### 2026-09-01 → 09-06 — Documentation pass
README expanded to the current structure (architecture, V2 spec, ERR log, iteration log,
risk table, milestones); v-photos; wiring diagrams + PCB render; 3D models; Open Challenge
video and YouTube link; milestone journey.
`3955cf3` · `5eee9a2` · `a4379be` · `0bb3fd1` · `baaa2da` · `eca476b`.

---

## Open items (as of 2026-09-06)

| Item | Milestone | State |
|---|---|---|
| *Mine vs. beyond the corner* classification — a can seen over the corner is sometimes assigned to the wrong straight | M10 | **Current focus** — `ERR-09`, open |
| Parking maneuver inside the bay | M11 | Not started — after M10 |
| Merge `SectionTurning` / `Workin` to `main` once track-tuned | M9 | On branch |
| Evidence backlog: per-run video + SHA for the 10 Open runs; RECUPERANDO true/false-fire tally; obstacle clean-run ratio | M8, M9 | Pending |

---

## How this journal is maintained

- New entry at the bottom of the current phase, dated, with the **why** and the **measured
  result** — not just what changed.
- When a change lands on `main`, add the commit short-hash. Branch work is labelled
  **branch** until merged.
- [README §5.3](README.md#53-iteration-log) stays the thematic summary; this file is the
  timeline. Keep them consistent when either changes.

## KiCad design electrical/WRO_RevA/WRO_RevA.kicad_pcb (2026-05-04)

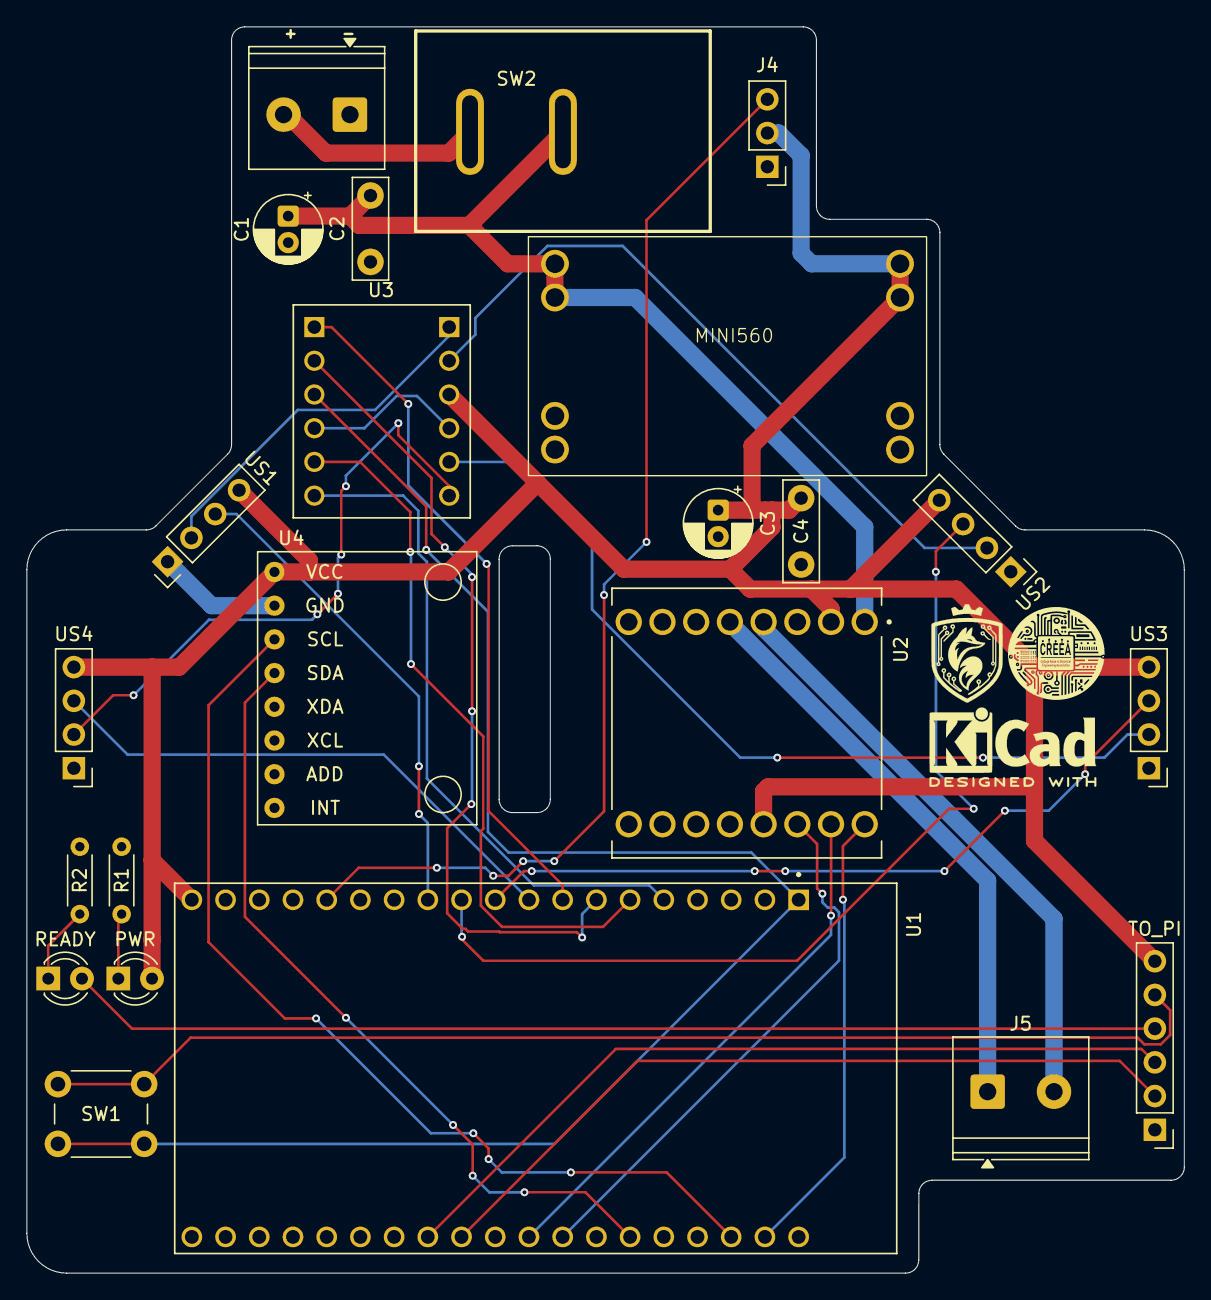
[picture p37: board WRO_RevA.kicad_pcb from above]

Board: 2 copper layers, 87.2 x 93.9 mm, 23 parts (0 on the bottom side), 31 nets.

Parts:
C1: 470uF; CP_Radial_D5.0mm_P2.00mm
C2, C4: 0.1uF; C_Disc_D7.5mm_W2.5mm_P5.00mm
C3: 100uF; CP_Radial_D5.0mm_P2.00mm
J1: VCC; TerminalBlock_Phoenix_PT-1,5-2-5.0-H_1x02_P5.00mm_Horizontal
J4: SERVO; PinHeader_1x03_P2.54mm_Vertical
J5: MOTOR; TerminalBlock_Phoenix_PT-1,5-2-5.0-H_1x02_P5.00mm_Horizontal
MINI560: V1; Mini560
PWR: PWR; LED_D3.0mm
R1, R2: 330; R_Axial_DIN0204_L3.6mm_D1.6mm_P5.08mm_Horizontal
READY: READY; LED_D3.0mm
SW1: EXEC_PRGM; SW_PUSH_6mm
SW2: PWR; SW-TH_L22.2-W15.0-P7.00_KCD1-2P-P
TO_PI: TO_PI; PinHeader_1x06_P2.54mm_Vertical
U1: ESP32-DEVKITC-32D
U2: ROB-14450; MODULE_ROB-14450
U3: BOB-12009; CONV_BOB-12009
U4: MPU6050; module_mpu6050
US1, US2, US3, US4: ULTRASONIC; PinHeader_1x04_P2.54mm_Vertical

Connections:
+3V3: SW1.1 (A), U1.J2-1 (3V3), U3.LV
+5V: C3.1, C4.1, J4.2, MINI560.3 (output+), PWR.2 (A), TO_PI.6, U1.J2-19 (EXT_5V), U2.2 (VCC), U2.13 (STBY), U3.HV, U4.1 (VCC), US1.4, US2.4, US3.4, US4.4
+11.2V: C1.1, C2.2, MINI560.1 (Input+), SW2.2, U2.1 (VM)
AIN1: U1.J3-8 (IO19), U2.14 (AI1)
AIN2: U1.J3-9 (IO18), U2.15 (AI2)
ECHO1: U3.HV1, US1.2
ECHO1_L: U1.J2-8 (IO33), U3.LV1
ECHO2: U3.HV2, US2.2
ECHO2_L: U1.J2-7 (IO32), U3.LV2
ECHO3: U3.HV3, US3.2
ECHO3_L: U1.J2-6 (IO35), U3.LV3
ECHO4: U3.HV4, US4.2
ECHO4_L: U1.J2-5 (IO34), U3.LV4
GND: C1.2, C2.1, C3.2, C4.2, J1.1, J4.1, MINI560.2 (input-), MINI560.4 (output-), R1.2, R2.2, TO_PI.1, U1.J2-14 (GND1), U1.J3-1 (GND3), U1.J3-7 (GND2), U2.3 (GND), U2.8 (GND), U2.9 (GND), U3.GND_1 (GND), U3.GND_2 (GND), U4.2 (GND), US1.1, US2.1, US3.1, US4.1
MOTOR_1: J5.2, U2.4 (A01)
MOTOR_2: J5.1, U2.5 (A02)
unnamed: PWR.1 (K), R1.1
unnamed: R2.1, READY.1 (K)
unnamed: J1.2, SW2.1
PRGM: SW1.2 (B), TO_PI.5
PWM_MOTOR: U1.J3-2 (IO23), U2.16 (PWMA)
READY: READY.2 (A), TO_PI.4
RX: TO_PI.3, U1.J3-12 (IO16)
SCL: U1.J3-3 (IO22), U4.3 (SCL)
SDA: U1.J3-6 (IO21), U4.4 (SDA)
SERVO: J4.3, U1.J2-15 (IO13)
TRIG1: U1.J2-12 (IO14), US1.3
TRIG2: U1.J2-11 (IO27), US2.3
TRIG3: U1.J2-10 (IO26), US3.3
TRIG4: U1.J2-9 (IO25), US4.3
TX: TO_PI.2, U1.J3-11 (IO17)

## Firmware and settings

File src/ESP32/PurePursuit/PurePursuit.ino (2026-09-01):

/*
 * PurePursuit.ino — WRO Future Engineers
 * Firmware ESP32 con soporte de protocolo V2 (Pure Pursuit desde Raspberry Pi).
 *
 * Basado en Controller_PI.ino. Diferencias respecto a la versión anterior:
 *   1. Parseo del campo pp= en mensajes V2.
 *   2. Cuando piPurePursuit=true:
 *        - Se suspende el PID de paredes (ultrasonidos).
 *        - La Pi envía obs=steer_deg/35 → ESP32 aplica ppSteerGain=35.
 *        - Solo se mantiene una corrección liviana de gyro para estabilizar heading.
 *   3. Cuando piPurePursuit=false (V1 o pp=0):
 *        - Comportamiento idéntico a Controller_PI.ino.
 *   4. Timeout de Pi (>800 ms sin mensaje):
 *        - Fallback a wall PID + gyro (igual que antes).
 *
 * PINES (sin cambios):
 *   HC-SR04 izq  : TRIG=27, ECHO=32
 *   HC-SR04 der  : TRIG=26, ECHO=35
 *   Motor DC     : PWMA=23, A1=18, A2=19  (TB6612FNG)
 *   Servo SG90   : SERVO_PIN=13
 *   MPU-6050     : I2C (SDA/SCL por defecto)
 *   Serial Pi    : Serial2 RX=17, TX=16 @ 115200
 */

#include <Wire.h>
#include <MPU6050_tockn.h>

MPU6050 mpu(Wire);

// ── Pines ─────────────────────────────────────────────────────────────────────
#define TRIG_L      27
#define ECHO_L      32
#define TRIG_R      26
#define ECHO_R      35

#define PWMA        23
#define A1          18
#define A2          19
#define SERVO_PIN   13

// ── PWM ───────────────────────────────────────────────────────────────────────
const int freqServo  = 50;
const int resServo   = 16;
const int freqMotor  = 1000;
const int resMotor   = 8;

// ── PID Paredes (ultrasónicos) ────────────────────────────────────────────────
float KpWall = 1.0;
float KiWall = 0.0;
float KdWall = 1.2;

float errorWall    = 0;
float prevErrorWall = 0;
float integralWall  = 0;

// ── PID Gyro ──────────────────────────────────────────────────────────────────
float KpGyro = 2.0;
float KiGyro = 0.0;
float KdGyro = 0.5;
float gyroScale = 1;

float errorGyro     = 0;
float prevErrorGyro = 0;
float integralGyro  = 0;

// ── Tiempo ────────────────────────────────────────────────────────────────────
unsigned long lastPIDTime  = 0;
unsigned long lastGyroTime = 0;

// ── Giroscopio ────────────────────────────────────────────────────────────────
float anguloGyro    = 0;
float anguloObjetivo = 0;

// ── Control ───────────────────────────────────────────────────────────────────
int velocidadMotor = 180;
int centroServo    = 80;

// ── Integración Pi → ESP32 ───────────────────────────────────────────────────
float obsBiasNorm  = 0.0;     // obs  [-1, 1] del mensaje V2
int   turnHint     = 0;       // turn {-1, 0, +1}
bool  piPriority   = false;   // prio=1: obstáculo activo en Pi
int   piMemoryFrames = 0;     // mem=N: frames de memoria restantes
bool  piPurePursuit = false;  // pp=1: Pi en modo Pure Pursuit
bool  piPasado     = false;   // pasado=1: la Pi confirma que un obstáculo quedó
                               // FÍSICAMENTE detrás del robot este frame (no que
                               // simplemente dejó de verlo) — dispara RECUPERANDO.
bool  piInteriorPass = false; // intr=1: el obstáculo actual se pasa por el mismo
                               // lado hacia el que va a girar la pista (la Pi ya
                               // sabe la dirección de giro, por visión, y el color
                               // del obstáculo) — el giro mismo resuelve el paso,
                               // no hace falta seguir bloqueando detectarEsquina().
bool  piReady      = false;

unsigned long lastPiMsgMs = 0;
const unsigned long piTimeoutMs = 800;  // ms sin mensaje → fallback

// Ganancia de visión V1 (modo fallback / obstáculo)
float visionSteerGain = 80.0;
float turnHintGain    = 7.0;

// Ganancia Pure Pursuit: obs = steer_deg / 35 → steerDeg = obs * 35 = steer_deg
const float ppSteerGain = 60.0;

// Cuánto se deflecta el servo por cada grado de PP.  steerDeg sale de la
// geometría (máx ±35°) y suele quedar corto para la mecánica del servo:
// súbelo si el carrito gira poco, bájalo si oscila/sobregira.
float ppServoGain = 1.0;
float PP_GYRO_BLEND = 0.4;   // 0 = solo vision, 1 = solo gyro. Empieza bajo y sube si sigue derivando.
float PP_WALL_BLEND = .15;

// ── Boot sincronización con Pi ────────────────────────────────────────────────
bool piReadyReceived = false;
// READY ya llegó PERO todavía no el primer V2. Entre esos dos, controlPID()
// caía en el fallback wall-PID y setMotor(velocidadMotor) -> el carro rodaba
// ~0.5 s hacia adelante sin ver el obstáculo. Con este gate el carro NO rueda
// hasta el primer V2 real de Pure Pursuit.
bool piFirstV2Received = false;
unsigned long readyMs = 0;                          // millis() cuando llegó READY
const unsigned long FIRST_V2_TIMEOUT_MS = 3000;     // si tras READY nunca llega V2, seguir igual
unsigned long bootStartMs = 0;
const unsigned long BOOT_WAIT_PI_MS = 1000;

// ── FSM estados ───────────────────────────────────────────────────────────────
// RECUPERANDO: la Pi confirma (piPasado=1) que el robot YA atravesó
// físicamente un obstáculo — no que la cámara simplemente dejó de verlo
// (perder de vista ≠ haber rebasado). En vez de que Pure Pursuit intente
// enderezar solo con lo que ve en ese instante incierto, aquí el wall PID +
// gyro PID (que YA se calculan siempre, ver controlPID()) toman el volante
// hasta que el robot vuelve a estar centrado/alineado.
enum Estado { SIGUIENDO, RECUPERANDO, GIRANDO };
Estado estado = SIGUIENDO;

const float wallSettleCm    = 8.0;   // |distL-distR| por debajo de esto = "centrado"
const float headingSettleDeg = 8.0;  // |errorGyro| por debajo de esto = "alineado"

// Red de seguridad: si el robot entra a RECUPERANDO cerca de una esquina real
// (donde un ultrasónico lee "sin pared" legítimamente, no por desalineación),
// wallOk puede no cumplirse NUNCA y el estado se quedaría atorado para siempre.
// Este timeout fuerza la salida aunque wallOk/headingOk no se hayan cumplido.
unsigned long recuperandoEntryMs = 0;
const unsigned long recuperandoTimeoutMs = 1500;

// ── Giros ─────────────────────────────────────────────────────────────────────
bool direccionIzquierda = true;
bool primerGiro         = false;
int  AngGiro            =88;
unsigned long lastTurnTime = 0;
int timeStart = 0;
const int cooldownGiro     = 2000;   // ms entre giros

// ── Detección de esquinas ─────────────────────────────────────────────────────
int contadorEsquina    = 0;
const int umbralPared  = 100;   // cm — pared "desaparece" → esquina
const int esquinaDebounce = 2;  // lecturas consecutivas antes de confiar (evita
                                 // falsos positivos por reflexión rasante del
                                 // ultrasónico cuando el chasis yawea fuerte)

// ── Carrera ───────────────────────────────────────────────────────────────────
int  turnsCompleted      = 0;
bool raceFinished        = false;
const int TURNS_PER_RACE = 12;

// ── Filtro EMA para ultrasonidos ──────────────────────────────────────────────
float alpha         = 0.85;
float distL_filtrada = 0;
float distR_filtrada = 0;


// ═══════════════════════════════════════════════════════════════════════════════
// Actuadores
// ═══════════════════════════════════════════════════════════════════════════════

void escribirServo(int angulo) {
  angulo = constrain(angulo, 0, 180);
  int pulso = map(angulo, 0, 180, 500, 2500);
  int duty  = (pulso * ((1 << resServo) - 1)) / 20000;
  ledcWrite(SERVO_PIN, duty);
}

void setMotor(int velocidad) {
  velocidad = constrain(velocidad, 0, 100);
  ledcWrite(PWMA, velocidad);
}


// ═══════════════════════════════════════════════════════════════════════════════
// Sensores
// ═══════════════════════════════════════════════════════════════════════════════

long leerDistancia(int trig, int echo) {
  digitalWrite(trig, LOW);
  delayMicroseconds(2);
  digitalWrite(trig, HIGH);
  delayMicroseconds(10);
  digitalWrite(trig, LOW);

  long dur  = pulseIn(echo, HIGH, 7000);
  long dist = dur * 0.034 / 2;
  if (dist == 0 || dist > 200) dist = 200;
  return dist;
}

float filtroEMA(float nueva, float anterior) {
  return alpha * nueva + (1.0 - alpha) * anterior;
}

void actualizarGyro() {
  unsigned long now = millis();
  float dt = (now - lastGyroTime) / 1000.0;
  lastGyroTime = now;

  float gz = mpu.getGyroZ() / gyroScale;
  if (abs(gz) < 1.0) gz = 0;
  anguloGyro += gz * dt;
}

bool detectarEsquina(long distL, long distR) {
  bool apertura = (distL > umbralPared) || (distR > umbralPared);
  if (apertura) contadorEsquina++;
  else          contadorEsquina = 0;
  return contadorEsquina >= esquinaDebounce;
}


// ═══════════════════════════════════════════════════════════════════════════════
// Protocolo serial con Raspberry Pi
// ═══════════════════════════════════════════════════════════════════════════════

void parsePiMessage(String line) {
  line.trim();

  // ── Handshake ──────────────────────────────────────────────────────────────
  if (line.startsWith("READY")) {
    piReadyReceived = true;
    piReady         = true;
    lastPiMsgMs     = millis();
    if (readyMs == 0) readyMs = millis();
    Serial2.println("ACK:READY");
    return;
  }

  // ── Protocolo V2 (Pure Pursuit) y V1 (obstáculo) ─────────────────────────
  // Formato: V2,obs=+0.350,turn=0,state=pp_follow,prio=0,mem=0,pp=1
  //      o:  V1,obs=+0.123,turn=0,state=avoid_red,prio=1,mem=18,pp=0
  //          (ambos se parsean igual — solo difiere el campo pp=)
  if (line.startsWith("V1,") || line.startsWith("V2,")) {

    // obs
    int idx = line.indexOf("obs=");
    if (idx >= 0) {
      int end = line.indexOf(',', idx);
      String s = (end >= 0) ? line.substring(idx + 4, end) : line.substring(idx + 4);
      obsBiasNorm = constrain(s.toFloat(), -1.0, 1.0);
    }

    // turn
    idx = line.indexOf("turn=");
    if (idx >= 0) {
      int end = line.indexOf(',', idx);
      String s = (end >= 0) ? line.substring(idx + 5, end) : line.substring(idx + 5);
      int v = s.toInt();
      turnHint = (v > 0) ? 1 : (v < 0) ? -1 : 0;
    }

    // prio
    idx = line.indexOf("prio=");
    if (idx >= 0) {
      int end = line.indexOf(',', idx);
      String s = (end >= 0) ? line.substring(idx + 5, end) : line.substring(idx + 5);
      piPriority = (s.toInt() != 0);
    }

    // mem
    idx = line.indexOf("mem=");
    if (idx >= 0) {
      int end = line.indexOf(',', idx);
      String s = (end >= 0) ? line.substring(idx + 4, end) : line.substring(idx + 4);
      piMemoryFrames = max(0L, s.toInt());
    }

    // pp  — campo nuevo en V2; ausente en mensajes V1 → pp=false por defecto
    idx = line.indexOf(",pp=");
    if (idx >= 0) {
      String s = line.substring(idx + 4);
      // solo toma el dígito antes de cualquier coma extra
      int end = s.indexOf(',');
      if (end >= 0) s = s.substring(0, end);
      piPurePursuit = (s.toInt() != 0);
    } else {
      piPurePursuit = false;   // mensaje V1 sin campo pp → modo obstáculo
    }

    // pasado — evento de un solo frame: el robot ya atravesó físicamente el
    // obstáculo. Ausente en V1 → false por defecto.
    idx = line.indexOf("pasado=");
    if (idx >= 0) {
      int end = line.indexOf(',', idx);
      String s = (end >= 0) ? line.substring(idx + 7, end) : line.substring(idx + 7);
      piPasado = (s.toInt() != 0);
    } else {
      piPasado = false;
    }

    // intr — el obstáculo actual se pasa por el mismo lado hacia el que va
    // a girar la pista (ver corner_lines.py en la Pi). Ausente en V1 o si
    // la Pi aún no confirmó la dirección de giro → false por defecto
    // (mismo comportamiento de siempre: sigue bloqueando).
    idx = line.indexOf("intr=");
    if (idx >= 0) {
      int end = line.indexOf(',', idx);
      String s = (end >= 0) ? line.substring(idx + 5, end) : line.substring(idx + 5);
      piInteriorPass = (s.toInt() != 0);
    } else {
      piInteriorPass = false;
    }

    piReady           = true;
    piFirstV2Received  = true;   // desde aquí el carro ya puede rodar
    lastPiMsgMs = millis();
    // Regresamos el heading integrado del gyro para que la Pi pueda mantener
    // su mapa rodante de obstáculos alineado al doblar (obstacle_memory.py).
    Serial2.print("ACK:V2,ang=");
    Serial2.print(anguloGyro, 2);
    Serial2.print(",est=");
    Serial2.print(estado == GIRANDO ? "G" : (estado == RECUPERANDO ? "R" : "S"));
    // Dirección de giro de la pista: '?' hasta el 1er GIRANDO, luego L/R
    // (direccionIzquierda se fija ahí con distL>distR). La Pi la usa para el
    // manejo de conos exteriores de esquina — fiable de la esquina 2 en
    // adelante (la 1 la sigue estimando por visión). primerGiro arranca en
    // false cada corrida porque el ESP se resetea entre runs.
    Serial2.print(",dir=");
    Serial2.println(!primerGiro ? "?" : (direccionIzquierda ? "L" : "R"));
    return;
  }

  // ── Modo legado: solo píxel X (controlPI.py original) ─────────────────────
  bool numeric = true;
  for (unsigned int i = 0; i < line.length(); i++) {
    char c = line.charAt(i);
    if (!(c >= '0' && c <= '9')) { numeric = false; break; }
  }
  if (numeric && line.length() > 0) {
    int x = line.toInt();
    if (x >= 0 && x <= 640) {
      obsBiasNorm   = constrain((float(x) - 320.0) / 320.0, -1.0, 1.0);
      piPurePursuit = false;
      piReady       = true;
      lastPiMsgMs   = millis();
      Serial2.println("ACK:X");
    }
  }
}

void readPiSerial() {
  while (Serial2.available() > 0) {
    String line = Serial2.readStringUntil('\n');
    if (line.length() > 0) parsePiMessage(line);
  }
}


// ═══════════════════════════════════════════════════════════════════════════════
// PID + control de servo
// ═══════════════════════════════════════════════════════════════════════════════
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
void loop() {
  readPiSerial();

  // Espera boot si la Pi todavía no respondió
  if (!piReadyReceived) {
    if ((millis() - bootStartMs) < BOOT_WAIT_PI_MS) {
      escribirServo(centroServo);
      setMotor(0);
      Serial.println(" | Estado:WAIT_PI");
      delay(20);
      return;
    }
    // Pasó el timeout de arranque → continuar de todas formas
  }

  // READY llegó PERO todavía no el primer V2 -> NO rodar. Si no, controlPID()
  // cae en el fallback wall-PID y el carro avanza ~0.5 s sin ver el obstáculo.
  // Con la Pi mandando el primer V2 justo tras READY, esto son unos ms; el
  // timeout evita quedar atorado para siempre si la Pi muere tras el READY.
  if (piReadyReceived && !piFirstV2Received
      && (millis() - readyMs) < FIRST_V2_TIMEOUT_MS) {
    escribirServo(centroServo);
    setMotor(0);
    Serial.println(" | Estado:WAIT_FIRST_V2");
    delay(10);
    return;
  }

  if (raceFinished) {
    setMotor(0);
    escribirServo(centroServo);
    Serial.println(" | TERMINADO giros=12/12");
    delay(20);
    return;
  }

  mpu.update();
  actualizarGyro();

  long distL_raw = leerDistancia(TRIG_L, ECHO_L);
  long distR_raw = leerDistancia(TRIG_R, ECHO_R);
  distL_filtrada = filtroEMA(distL_raw, distL_filtrada);
  distR_filtrada = filtroEMA(distR_raw, distR_filtrada);

  long distL = (long)distL_filtrada;
  long distR = (long)distR_filtrada;

  switch (estado) {

    case SIGUIENDO: {
      velocidadMotor = 180;

      // La Pi confirma que el robot ya atravesó físicamente el obstáculo
      // (evento de un solo frame) -> entrar a RECUPERANDO. Ya no depende de
      // que la cámara simplemente haya dejado de verlo.
      if (piPasado) {
        estado = RECUPERANDO;
        recuperandoEntryMs = millis();
        integralWall  = 0; prevErrorWall  = 0;
        integralGyro  = 0; prevErrorGyro  = 0;

        // Consumir el pulso.  piPasado es un evento de UN frame en la Pi, pero
        // en el ESP32 se queda en 1 hasta que llega el siguiente mensaje V2
        // (~70-150 ms) y el loop() corre cientos de veces en ese lapso.  Sin
        // esto, si RECUPERANDO sale rápido (headingOk ya se cumple porque el
        // rebase fue casi recto), SIGUIENDO vuelve a entrar a RECUPERANDO en la
        // iteración siguiente con el MISMO pulso viejo -> rebote de estado y
        // reseteo repetido de integrales / patada en la derivada del servo.
        // Un rebase nuevo real llega en otro mensaje y vuelve a poner piPasado=1.
        piPasado = false;

        controlPID(distL, distR);   // ya toma el branch RECUPERANDO (estado ya cambió)
        break;
      }

      controlPID(distL, distR);

      // No girar si hay obstáculo activo en Pi.  (El gate de heading ya no
      // hace falta aquí — mientras el chasis sigue desalineado, ese trabajo
      // lo hace el estado RECUPERANDO, que ni siquiera llega a evaluar
      // detectarEsquina() porque vive en otro case del switch.)
      // Excepción: si el obstáculo se pasa por el mismo lado hacia el que
      // ya se sabe que va a girar la pista (piInteriorPass), el giro mismo
      // resuelve el paso — no tiene caso seguir bloqueando. piInteriorPass
      // es false por defecto (sin dirección confirmada aún, o exterior),
      // así que sin eso el comportamiento es idéntico al de siempre.
      bool bloqueadoPorObstaculo = (piPriority || (piMemoryFrames > 0)) && !piInteriorPass;

      // 2026-08-28: gate de alineación. En un latiguazo de esquiva el chasis
      // queda ladeado (visto en pista a +37deg) y un ultrasónico lateral lee
      // "sin pared" -> detectarEsquina() disparaba una falsa esquina.
      // 25° (no 15): con 15 el carro no lograba mantenerse recto y NO detectaba
      // la esquina real -> se iba de frente. 25 bloquea el latiguazo (37°) pero
      // permite esquinas reales con algo de error de heading. (Con
      // INTERIOR_PASS_ENABLED=False el bloqueo por obstáculo ya tapa el caso
      // original; esto es red de seguridad.)
      bool chasisAlineado = fabs(anguloGyro) < 25.0f;

      if ((millis() - lastTurnTime > cooldownGiro)
          && !bloqueadoPorObstaculo
          && detectarEsquina(distL, distR)
          && millis() - timeStart > 3000)
      {
        estado     = GIRANDO;
        anguloGyro = 0;

        if (!primerGiro) {
          direccionIzquierda = (distL > distR);
          primerGiro         = true;
        }

        // Suspender PP durante el giro — el servo lo controla GIRANDO
        piPurePursuit = false;

        Serial.println(direccionIzquierda ? "Giro izquierda" : "Giro derecha");
      }
      break;
    }

    case RECUPERANDO: {
      velocidadMotor = 180;
      controlPID(distL, distR);   // toma el branch RECUPERANDO de controlPID()

      bool wallOk    = abs(errorWall) < wallSettleCm;
      bool headingOk = abs(errorGyro) < headingSettleDeg;
      bool timedOut  = (millis() - recuperandoEntryMs) > recuperandoTimeoutMs;

      if (piPriority) {
        // Reapareció un obstáculo (o uno nuevo) → vuelve a esquivar
        estado = SIGUIENDO;
      } else if ((headingOk)) {
        // Ya centrado y alineado → visión retoma el control normal.
        // timedOut: red de seguridad si wallOk nunca se cumple (p.ej. cerca
        // de una esquina real, donde un lado lee "sin pared" legítimamente).
        estado = SIGUIENDO;
      }
      break;
    }

    case GIRANDO: {
      float delta = abs(anguloGyro);

      if      (delta < 45) velocidadMotor = 165;
      else if (delta < 70) velocidadMotor = 145;
      else                 velocidadMotor = 120;

      setMotor(velocidadMotor);
      escribirServo(direccionIzquierda ? 150 : 20);

      if (delta >= AngGiro) {
        escribirServo(centroServo);
        velocidadMotor = 180;

        // Resetear integrales
        integralWall = 0; prevErrorWall = 0;
        integralGyro = 0; prevErrorGyro = 0;

        anguloObjetivo = anguloGyro;
        lastTurnTime   = millis();
        estado         = SIGUIENDO;
        turnsCompleted++;

        if (turnsCompleted >= TURNS_PER_RACE) {
          raceFinished = true;
        }

        Serial.print("Giro completado ");
        Serial.print(turnsCompleted);
        Serial.print("/");
        Serial.println(TURNS_PER_RACE);
      }
      break;
    }
  }

  // ── Log periódico ─────────────────────────────────────────────────────────
  Serial.print(" | Estado:");
  if      (estado == GIRANDO)     Serial.print("GIRANDO");
  else if (estado == RECUPERANDO) Serial.print("RECUPERANDO");
  else                             Serial.print("SIGUIENDO");
  Serial.print(" | PP:");       Serial.print(piPurePursuit ? 1 : 0);
  Serial.print(" | L:");        Serial.print(distL);
  Serial.print(" | R:");        Serial.print(distR);
  Serial.print(" | Ang:");      Serial.print(anguloGyro);
  Serial.print(" | Obj:");      Serial.print(anguloObjetivo);
  Serial.print(" | obs:");      Serial.print(obsBiasNorm, 3);
  Serial.print(" | turn:");     Serial.print(turnHint);
  Serial.print(" | prio:");     Serial.print(piPriority ? 1 : 0);
  Serial.print(" | mem:");      Serial.print(piMemoryFrames);
  Serial.print(" | intr:");     Serial.print(piInteriorPass ? 1 : 0);
  Serial.print(" | giros:");    Serial.print(turnsCompleted);
  Serial.print("/");            Serial.println(TURNS_PER_RACE);
}

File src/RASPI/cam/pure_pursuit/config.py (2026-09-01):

"""
Parámetros de configuración del pipeline Pure Pursuit — WRO Future Engineers.

Hardware:
  Cámara  : Raspberry Pi Camera v2  (FOV ~62°, resolución proceso 640×480)
  Motor   : N20 DC 50:1 + etapa LEGO 2:1  → ratio total 100:1
  Servo   : SG90  (centro = 80°, límite mecánico ±35° efectivo en rueda)
  Chassis : 210×140×80 mm  |  batalla ~100 mm (estimado)
  ESP32   : recibe protocolo V2 por UART Serial2 (RX=17, TX=16) @ 115200
  Pi GPIO : LED en 27, botón arranque en 17

Ajusta primero CALIB_REAL_MM para que coincida con tu montaje de cámara,
luego corre calibrate.py para generar bev_calib.npz.
"""

import numpy as np
from pathlib import Path

# ─── Rutas ────────────────────────────────────────────────────────────────────
CALIB_FILE = Path(__file__).parent / "bev_calib.npz"

# ─── BEV — imagen de salida ───────────────────────────────────────────────────
BEV_W      = 400          # píxeles de ancho
BEV_H      = 400          # píxeles de alto
MM_PER_PX  = 2.0          # escala: 1px = 2 mm  →  400px = 800 mm de cobertura

# Posición del robot en la imagen BEV (eje trasero, centro horizontal)
ROBOT_BEV_X = BEV_W // 2   # 200
ROBOT_BEV_Y = BEV_H - 20   # 380

# ─── Puntos de calibración en el suelo (mm, relativo a eje delantero del robot) ──
# x_mm: lateral  (+ = derecha del robot)
# y_mm: distancia hacia adelante desde el eje delantero
#
# IMPORTANTE — por qué 9 puntos y no 4:
#   Una homografía con exactamente 4 puntos es un ajuste EXACTO: no hay forma
#   de detectar ni corregir un clic impreciso durante la calibración, y la
#   transformación se vuelve muy poco confiable fuera del área que cubren esos
#   4 puntos (extrapolación agresiva).  Con 9 puntos en grilla 3×3,
#   cv2.findHomography(..., RANSAC) puede promediar/filtrar el ruido de los
#   clics, y el área cubierta coincide con el rango real que usa
#   centerline.py (desde muy cerca del robot hasta ~550mm adelante).
#
#   Coloca marcadores físicos en el suelo en estas posiciones exactas y haz
#   clic en ellos EN ESTE MISMO ORDEN dentro de calibrate.py.
#
#          izquierda        centro         derecha
#   lejos:   P7 (-220,550)  P8 (0,550)   P9 (220,550)
#   media:   P4 (-150,300)  P5 (0,300)   P6 (150,300)
#   cerca:   P1  (-80, 80)  P2 (0, 80)   P3  (80, 80)
CALIB_REAL_MM = np.float32([
    [ -80.0,  80.0],   # P1: cerca-izquierda
    [   0.0,  80.0],   # P2: cerca-centro
    [  80.0,  80.0],   # P3: cerca-derecha
    [-150.0, 300.0],   # P4: media-izquierda
    [   0.0, 300.0],   # P5: media-centro
    [ 150.0, 300.0],   # P6: media-derecha
    [-220.0, 550.0],   # P7: lejos-izquierda
    [   0.0, 550.0],   # P8: lejos-centro
    [ 220.0, 550.0],   # P9: lejos-derecha
])

# Etiquetas legibles para cada punto (mismo orden que CALIB_REAL_MM)
CALIB_POINT_LABELS = [
    "P1 cerca-izq", "P2 cerca-centro", "P3 cerca-der",
    "P4 media-izq", "P5 media-centro", "P6 media-der",
    "P7 lejos-izq", "P8 lejos-centro", "P9 lejos-der",
]

# Umbral de error medio de reproyección (px BEV) a partir del cual calibrate.py
# advierte que probablemente un clic quedó mal puesto.
CALIB_MAX_MEAN_ERR_PX = 4.0

WALL_MARGIN_PX = 22

# ─── Color del piso (HSV) — tapete WRO: beige / madera cálida ────────────────
FLOOR_LOWER = np.array([0, 0, 140])
FLOOR_UPPER = np.array([35, 80, 255])

FLOOR_LOWER_BLUE = np.array([95, 50, 10])
FLOOR_UPPER_BLUE = np.array([150, 255, 220])

FLOOR_LOWER_BLUE_WIDE = np.array([90, 15, 60])   # baja el mínimo de S y sube V
FLOOR_UPPER_BLUE_WIDE = np.array([150, 255, 230])

WALL_STRUCTURE_PX = 15   # <-- ajusta viendo tu imagen BEV real

FLOOR_LOWER_ORANGE = np.array([1,  70, 130])
FLOOR_UPPER_ORANGE = np.array([17, 160, 220])

# Lista usada por centerline.py — agrega más tuplas aquí si detectas más
# colores de piso que no quieres que bloqueen la ruta.
FLOOR_COLOR_RANGES = [
    (FLOOR_LOWER, FLOOR_UPPER),
    (FLOOR_LOWER_BLUE, FLOOR_UPPER_BLUE),
    (FLOOR_LOWER_ORANGE, FLOOR_UPPER_ORANGE),
]
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

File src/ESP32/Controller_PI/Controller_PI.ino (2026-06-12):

#include <Wire.h>
#include <MPU6050_tockn.h>

MPU6050 mpu(Wire);

// PINES
#define TRIG_L 27
#define ECHO_L 32
#define TRIG_R 26
#define ECHO_R 35

#define PWMA 23
#define A1 18
#define A2 19
#define SERVO_PIN 13

// PWM
const int freqServo = 50;
const int resServo = 16;
const int freqMotor = 1000;
const int resMotor = 8;

// PID PAREDES
float KpWall = 1.0;
float KiWall = 0.0;
float KdWall = 1.2;

float errorWall = 0;
float prevErrorWall = 0;
float integralWall = 0;

// PID GYRO
float KpGyro = 2.0;
float KiGyro = 0.0;
float KdGyro = 0.5;
float gyroScale = 1;

float errorGyro = 0;
float prevErrorGyro = 0;
float integralGyro = 0;

// TIEMPO
unsigned long lastPIDTime = 0;
unsigned long lastGyroTime = 0;

// GIROSCOPIO
float anguloGyro = 0;
float anguloObjetivo = 0;

// CONTROL
int velocidadMotor = 180;
int centroServo = 80;

// INTEGRACION PI -> ESP32
float obsBiasNorm = 0.0;     // [-1, 1]
int turnHint = 0;            // -1 derecha, 0 ninguno, +1 izquierda
unsigned long lastPiMsgMs = 0;
const unsigned long piTimeoutMs = 800;
bool piPriority = false;
int piMemoryFrames = 0;
bool piReady = false;
unsigned long bootStartMs = 0;

const bool WAIT_PI_AT_BOOT = true;
const bool ALLOW_FALLBACK_AFTER_WAIT = true;
const unsigned long BOOT_WAIT_PI_MS = 1000;

float visionSteerGain = 80.0;
float turnHintGain = 7.0;

// ESTADOS
enum Estado {
  SIGUIENDO,
  GIRANDO
};

Estado estado = SIGUIENDO;

// GIROS
bool direccionIzquierda = true;
bool primerGiro = false;
int AngGiro = 75;
unsigned long lastTurnTime = 0;
const int cooldownGiro = 1500;

// DETECCION
int contadorEsquina = 0;
const int umbralPared = 100;

// CARRERA
int turnsCompleted = 0;
bool raceFinished = false;
const int TURNS_PER_RACE = 12;

// FILTRO
float alpha = 0.85;
float distL_filtrada = 0;
float distR_filtrada = 0;

void printDual(String txt) {
  Serial.print(txt);
}

void escribirServo(int angulo) {
  angulo = constrain(angulo, 0, 180);
  int pulso = map(angulo, 0, 180, 500, 2500);
  int duty = (pulso * ((1 << resServo) - 1)) / 20000;
  ledcWrite(SERVO_PIN, duty);
}

void setMotor(int velocidad) {
  velocidad = constrain(velocidad, 0, 255);
  ledcWrite(PWMA, velocidad);
}

long leerDistancia(int trig, int echo) {
  digitalWrite(trig, LOW);
  delayMicroseconds(2);
  digitalWrite(trig, HIGH);
  delayMicroseconds(10);
  digitalWrite(trig, LOW);

  long duracion = pulseIn(echo, HIGH, 5000);
  long distancia = duracion * 0.034 / 2;

  if (distancia == 0 || distancia > 200) {
    distancia = 200;
  }

  return distancia;
}

float filtroEMA(float nueva, float anterior) {
  return alpha * nueva + (1.0 - alpha) * anterior;
}

bool detectarEsquina(long distL, long distR) {
  bool apertura = (distL > umbralPared) || (distR > umbralPared);
  if (apertura) {
    contadorEsquina++;
  } else {
    contadorEsquina = 0;
  }
  return contadorEsquina >= 1;
}

void actualizarGyro() {
  unsigned long now = millis();
  float dt = (now - lastGyroTime) / 1000.0;
  lastGyroTime = now;

  float gyroZ = mpu.getGyroZ()/gyroScale;
  if (abs(gyroZ) < 1.0) {
    gyroZ = 0;
  }

  anguloGyro += gyroZ * dt;
}

void parsePiMessage(String line) {
  line.trim();

  // Handshake de arranque: la Pi envia READY cuando termino de levantar.
  if (line.startsWith("READY")) {
    piReady = true;
    lastPiMsgMs = millis();
    Serial2.println("ACK:READY");
    return;
  }

  // Nuevo formato recomendado:
  // V1,obs=+0.123,turn=0,state=avoid_red
  if (line.startsWith("V1,")) {
    int obsIdx = line.indexOf("obs=");
    int turnIdx = line.indexOf("turn=");
    int prioIdx = line.indexOf("prio=");
    int memIdx = line.indexOf("mem=");

    if (obsIdx >= 0) {
      int obsEnd = line.indexOf(',', obsIdx);
      String obsStr = (obsEnd >= 0) ? line.substring(obsIdx + 4, obsEnd) : line.substring(obsIdx + 4);
      obsBiasNorm = obsStr.toFloat();
      obsBiasNorm = constrain(obsBiasNorm, -1.0, 1.0);
    }

    if (turnIdx >= 0) {
      int turnEnd = line.indexOf(',', turnIdx);
      String turnStr = (turnEnd >= 0) ? line.substring(turnIdx + 5, turnEnd) : line.substring(turnIdx + 5);
      int turnVal = turnStr.toInt();
      if (turnVal > 0) {
        turnHint = 1;
      } else if (turnVal < 0) {
        turnHint = -1;
      } else {
        turnHint = 0;
      }
    }

    if (prioIdx >= 0) {
      int prioEnd = line.indexOf(',', prioIdx);
      String prioStr = (prioEnd >= 0) ? line.substring(prioIdx + 5, prioEnd) : line.substring(prioIdx + 5);
      piPriority = (prioStr.toInt() != 0);
    }

    if (memIdx >= 0) {
      int memEnd = line.indexOf(',', memIdx);
      String memStr = (memEnd >= 0) ? line.substring(memIdx + 4, memEnd) : line.substring(memIdx + 4);
      piMemoryFrames = memStr.toInt();
      if (piMemoryFrames < 0) {
        piMemoryFrames = 0;
      }
    }

    piReady = true;
    lastPiMsgMs = millis();
    Serial2.println("ACK:V1");
    return;
  }

  // Modo legado: solo pixel X (como controlPI.py original)
  bool numeric = true;
  for (unsigned int i = 0; i < line.length(); i++) {
    char c = line.charAt(i);
    if (!(c >= '0' && c <= '9')) {
      numeric = false;
      break;
    }
  }

  if (numeric && line.length() > 0) {
    int x = line.toInt();
    // Convierte 0..640 a -1..1. Si llega 700 (neutral), cae cerca de +1, asi que saturamos por rango.
    if (x >= 0 && x <= 640) {
      obsBiasNorm = (float(x) - 320.0) / 320.0;
      obsBiasNorm = constrain(obsBiasNorm, -1.0, 1.0);
      piReady = true;
      lastPiMsgMs = millis();
      Serial2.println("ACK:X");
    }
  }
}

void readPiSerial() {
  while (Serial2.available() > 0) {
    String line = Serial2.readStringUntil('\n');
    if (line.length() > 0) {
      parsePiMessage(line);
    }
  }
}
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

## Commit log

2026-04-17 Cad model
    3d design of the vehicle
    [BaseDireccion.STL, Chasis.STL, Cremallera.STL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]
2026-04-17 added current progress of PCB
    [WRO_RevA.kicad_pcb, WRO_RevA.kicad_sch]
2026-04-17 schematic done
    [WRO_RevA.kicad_sch]
2026-04-17 added mods
    [WRO_RevA.kicad_pcb, WRO_RevA.kicad_sch]
2026-04-17 minor changes to PCB
    Lvl shifter still too big. have to mod ultrasonics....
    [WRO_RevA.kicad_pcb, WRO_RevA.kicad_sch]
2026-04-22 minor changes
    [WRO_RevA.kicad_pcb, WRO_RevA.kicad_sch]
2026-04-24 final shape for PCB, only need to route
    [WRO_RevA.kicad_pcb, WRO_RevA.kicad_sch]
2026-04-27 started routing, added CREEA logo
    gracias gustavo creea
    [WRO_RevA.kicad_pcb, WRO_RevA.kicad_sch]
2026-05-10 Working controller for no obstacle
    Controller changed, PID algorithm now uses Ultrasonic sensors and GyroZ angle for better precision
2026-05-23 mostrar lo que procesa nomas
2026-05-23 otro hilo para grabar
2026-05-23 limitar la grabacion del video
2026-05-25 Organized folder model
    Added the SolidWorks Cad model
    [BaseChasis.SLDPRT, BaseDireccion.STL, CameraBack.SLDPRT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]
2026-06-05 limpieza de codigos
2026-06-05 acomodar codigos que no se usan
2026-06-09 logs de mandar comandos
2026-06-09 agregando timeout para esperar a la pi
2026-06-12 FixedController for open challenge
    [Controller_PI.ino]
2026-06-22 cambios del error en duplicado de camara
    [calibrate.py, config.py, test_vision.py]
2026-06-23 algoritmo de center
2026-06-23 Revert "asdf"
    This reverts commit f218ca313c3b91f7bb542f6d89b101a688b00495.
    [PurePursuit.ino, config.py]
